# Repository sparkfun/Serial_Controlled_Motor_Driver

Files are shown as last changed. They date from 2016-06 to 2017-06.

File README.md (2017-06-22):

SparkFun Serial Controlled Motor Driver
=======================================

SparkFun Serial Controlled Motor Driver

[*SparkFun Serial Controlled Motor Driver (ROB-13911)*](https://www.sparkfun.com/products/13911)

The expandable SparkFun Serial Controlled Motor Driver allows you to control 2 DC motors using a serial command interface over I2C, SPI, or TTL UART. 

Features:
* User port configurable to SPI, I2C, or UART.
* Expansion port utalizing I2C that allows 16 additional drivers
* Auto-enumeration based on connection of expansion 'In' and 'Out' connections - First board becomes first slave in software.
* 1.5 A peak drive per channel
* Bridging mode for any one board to double current drive.
* Operates from 3 to 11 volts with 12v absolute max.
* Stock 3.3v operation of cpu and signals, with VCC breakable to allow up to 5.5v levels.

Repository Contents
-------------------
* **/Documentation** - Datasheet, test information, and diagrams
* **/Firmware** - PSoC projects of embedded firmware
* **/Hardware** - Eagle design files (.brd, .sch)
* **/Libraries** - Libraries for use with the motor driver
* **/Production** - Production files
* **/Software** - Arduino sketches and examples

Documentation
--------------
* **[Library](https://github.com/sparkfun/SparkFun_Serial_Controlled_Motor_Driver_Arduino_Library)** - Arduino library
* **[Hookup Guide](https://learn.sparkfun.com/tutorials/serial-controlled-motor-driver-hookup-guide)** - Basic hookup guide
* **[SparkFun Fritzing repo](https://github.com/sparkfun/Fritzing_Parts)** - Fritzing diagrams for SparkFun products.
* **[SparkFun 3D Model repo](https://github.com/sparkfun/3D_Models)** - 3D models of SparkFun products. 
* **[SparkFun Graphical Datasheets](https://github.com/sparkfun/Graphical_Datasheets)** -Graphical Datasheets for various SparkFun products.

Hardware Compatibility
----------------
* [ROB-13911](https://www.sparkfun.com/products/13911) - Serial controlled motor driver.
* [DEV-14213](https://www.sparkfun.com/products/14213) - SparkFun moto:bit (SCMD_FID_V07a.HEX).

Version History
---------------
* [HW_1.2_FW_1.2](https://github.com/sparkfun/Serial_Controlled_Motor_Driver/tree/HW_1.2_FW_1.2) - Original product
* [V_1.5](https://github.com/sparkfun/Serial_Controlled_Motor_Driver/tree/V_1.5) - Revision prototype 1
* [V_1.6](https://github.com/sparkfun/Serial_Controlled_Motor_Driver/tree/V_1.6) - Revision prototype 2
* [V_1.6.1](https://github.com/sparkfun/Serial_Controlled_Motor_Driver/tree/V_1.6.1) - Revision prototype 2 with non-zero width poly outlines and dev board version V_1.X
* [V_2.0](https://github.com/sparkfun/Serial_Controlled_Motor_Driver/tree/V_2.0) - Version 2.0 of product
* [V_2.0.1](https://github.com/sparkfun/Serial_Controlled_Motor_Driver/tree/V_2.0.1) - Compatible with moto:bit hardware.

License Information
-------------------

This product is _**open source**_! 

Please review the LICENSE.md file for license information. 

If you have any questions or concerns on licensing, please contact techsupport@sparkfun.com.

Distributed as-is; no warranty is given.

- Your friends at SparkFun.

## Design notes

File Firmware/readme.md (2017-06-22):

Contents
-----------

* SCMD_FW.cydsn -- Project folder for current version of firmware.
* Releases -- hex files for release
  * SCMD_FID_02.hex -- Internal release, lacks self diagnostics features
  * SCMD_FID_03.hex -- Beta release.  Final release features present.  Now has better failsafe, control of config_pin, bus rate control regs and is tested on all three interface modes.
  * SCMD_FID_04.hex -- Test mode for config pins added, enumeration status added, high speed uart modes added as jumper settings.
  * SCMD_FID_06.hex -- Production release.
  * SCMD_FID_07.hex -- Release for moto:bit compatibility.
  * SCMD_FID_07a.hex -- Production release for moto:bit compatibility.  Fixed enable pin bit (was b2, now is b4).

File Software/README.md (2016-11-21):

SparkFun Serial Controlled Motor Driver (SCMD) Software
=======================================

This software used to test the firmware and functions.  Users should see directory /Libraries (up one level) for example code and arduino libraries.

Contents:
-------------------
* /FailSafeTest/ -- Configures the SCMD into a mode to allow failsafe testing
* /FWFunctionalTest/ -- Automated portion of the functional test doc
* /testProgram/ -- Program used in product video with sliders

License Information
-------------------
The hardware is released under [Creative Commons ShareAlike 4.0 International](https://creativecommons.org/licenses/by-sa/4.0/).
The code is beerware; if you see me (or any other SparkFun employee) at the local, and you've found our code helpful, please buy us a round!

Distributed as-is; no warranty is given.

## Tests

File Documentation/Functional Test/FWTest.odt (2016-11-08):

# Buses

## Test the I2C user interface

This test checks all the ways a user can connect the I2C interface.

Procedure:

1. Test the following configurations:
  1. SCMD master at any lowest address, 100 kHz redboard Pass
  2. Two SCMD masters, one at highest address, 100 KHz redboard Pass
  3. 400 KHz on teensy (Low priority) Skipped
2. For each configuration, run the diag example and look for errors. Pass

Criteria:

1. Did the EUTs behave normally?? YES

## Test the SPI user interface

This test checks all the ways a user can connect the SPI interface.

Procedure:

1. Test the following configurations:
  1. SCMD master at 1 MHz Tested at 500kHz and 1 MHz, Pass
  2. Two SCMD masters with different CS pins. Pass
2. For each configuration, run the diag example and look for errors. Pass

Criteria:

2. Did the EUTs behave normally? YES

## Test the UART user interface

Procedure:

1. Test the following configurations:
  1. SCMD at default baud Pass
  2. SCMD at 57600 baud by jumper Pass
  3. SCMD at 115200 baud by jumper Pass
  4. Other configurations by using the commands U0-U7. Pass
2. Test that the number are accepted as 1 or two digit for most, and 3 for drive percent Pass
3. Test that enable is passed to slaves Pass
4. Test that E, B, and MxxS commands result in the proper bit flipped within INV_X_X, BRIDGE_SLV_X registers Pass

#define SCMD_INV_2_9 0x50

#define SCMD_INV_10_17 0x51

#define SCMD_INV_18_25 0x52

#define SCMD_INV_26_33 0x53

#define SCMD_BRIDGE_SLV_L 0x54

#define SCMD_BRIDGE_SLV_H 0x55

Criteria:

1. Did the EUTs behave normally?? YES

# FW elements

For these tests, connect 16 slaves and perform the following actions using the registerRWtool

## Test motor driving registers

Make sure motor information is passed to the correct locations

Procedure:

1. Test that the following motors drive when master locations are written: Pass
  1. motor 0,1, 2, 3, 4, 5, 17, 18, and 33

Criteria:

1. Do commands cause correct change on all motors? YES

## Test slave configuration

Test that writing to slave and global registers passes the information on to the slaves correctly. For these tests remote access is required by remote window or arduino function.

1. Motor 2, 9, 10, 17, 18, 25, 26 and 33 Pass
2. Bridge 0, 1, 8, 9, and 16 Pass

#define SCMD_MOTOR_A_INVERT 0x12

#define SCMD_MOTOR_B_INVERT 0x13

#define SCMD_BRIDGE 0x14

Procedure:

1. Write a pattern to INV regs and read remote local inversion regs. Pass
2. Write a pattern to BRIDGE regs and read remote local bridging regs Pass
3. Check that the following are passed directly (global config) to the associated local slave registers.
  1. DRIVER_ENABLE Pass
  2. MASTER_LOCK Pass
  3. USER_LOCK Pass
  4. FSAFE_TIME Pass

Criteria:

1. Are all values passed correctly? YES

## Check lock protections

Make sure the master and user locks operate

Procedure:

1. Write each "R" register with master key removed, then use REG_OOR_CNT to verify if they were protected Pass
2. Write each "user lock"able register with the user key removed, then use REG_OOR_CNT to verify they did not accept the data. Pass
3. Write each "user lock"able register with the user key inserted, REG_OOR_CNT should read 0. Pass
4. Write a new FID in with both keys inserted, and read back to verify. Pass

Criteria:

1. Were the locks capible of preventing or allowing the correct operations? YES

## Test the failsafe mode

This checks that all modes of failsafe operate

Procedure:

1. Probe config out and exp. data
2. Set the FSAFE_TIME(0x76) to 0xC8 for 2 second failsafe time Pass
3. Set FSAFE_CTRL:
  1. Use b1 for drive off/last behavior Pass
  2. Set 0x02 for reboot Pass
  3. Set 0x04 for re-enumerate. Pass
  4. Set 0x08 for user port re-init. Pass – works but doesn't recover data
  5. Set 0x10 for expansion port re-init Pass
4. Check the slave contents of FSAFE_TIME to determine if configuration was properly transfered during re-enumerate. Yes

Criteria:

1. Did the EUT recover as expected? Yes

## Test enumeration

Check that enumeration occurs correctly. For many of these, reading 0x0B for top address may be useful.

Procedure:

1. Check that enumeration occurs successfully for 0, 1, 2, and 16 slaves. Pass
2. Issue a reboot by CONTROL_1 for 16 Pass
3. Configure some global settings
4. Issue a re-enumeration by CONTROL_1 for 16 slaves
5. Check that global settings were correctly passed to slaves Pass
6. Configure master config in pin with MST_E_IN_FN and test function by shorting config_in to ground Pass

Criteria:

1. Does the top address match for various slaves? YES?
2. Do both reboots result in a proper enumeration? YES?
3. Do both reenumerations result in the correct configuration? YES?

## Test the expansion bus speed setting

Check that the expansion bus can be configured by inspecting with a scope.

Procedure:

1. Measure the bit rate of the defualt 100KHz setting
2. Configure and test the 50KHz and 400 KHz settings using E_BUS_SPEED
3. Measure the slave motor data packets dead time, and set UPDATE_RATE to change Pass
4. With UPDATE_RATE set to 0, does a packet occur after writing FORCE_UPDATE to 1? Pass

Criteria:

1. Are bus configuration parameters effecting operation properly? YES

## Test an item in the Test Plan

Describe the intent of the item to be tested

Procedure:

1. First step to testing
2. Second step to testing

Criteria:

1. Describe acceptable test results as a question? YES/NO

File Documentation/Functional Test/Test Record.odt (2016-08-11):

# Functional Test Record

## 1) Test thermal performance of the board and DRV8835

Determine temperature rise of board operating at max drive

Procedure:

1. Attach resistors to output channels such that they consume 1.5A at 11.0V supply
2. Attach termocouple to DRV8835
3. Lay EUT flat on FR4 "burn surface", or something with marginal thermal conductivity. Allow top-side convection.
4. Target FliR cam at EUT
5. Starting with low drive,
  1. Set drive level
  2. Measure current at that drive level
  3. Wait for EUT to stabilize
  4. Record final temperature of DRV8835
  5. Take a thermal picture
  6. Increment drive level

Criteria:

1. Unknown – Does EUT satisfy typical use cases? YES/NO

## 2) Input Voltage Range

Check that the EUT operates normally under the full voltage range of the product, under various loads

Procedure:

1. Attach current and voltage meters to input
2. Power the EUT with variable supply
3. Attach voltage monitor to VREG pin
4. Program the device to output 0.5A, 1A, 1.5 A total drive (channels combined)
5. Operate the drive on both channels while measuring the VREG pin, input current, and input voltage. Create a graph

Criteria:

1. Does the EUT function as expected? YES/NO
2. Is the output voltage liner to drive at all levels? YES/NO

## 3) Test Current Resistance in board

Determine if the PCB is limiting current to the board

Procedure:

1. Measure input voltage and current, apply 11.0V
2. Attach 11.0 V resistors to output terminals
3. Drive both outputs max each way.

Criteria:

1. Do both outputs deliver 1.5A? YES/NO

## 4) Test LDO power dissipation

Calculate the power dissipated by the LDO

Procedure:

1. Split the power out trace on the bottom of the board near the VREG pin, insert current meter
2. Measure voltage in, current in, voltage out(VREG), current out
3. Take measurements across voltage range in 1v increments
4. Produce a graph of the power consumed by the LDO

Criteria:

1. Is the power dissipated less than 1/4 watt? YES/NO

## 5) Determine resistance to back-EMF generated by manually pushed motors

Test that forcing the drive motors around during drive does not damage the EUT

Procedure:

1. Supply the EUT through a 0.5 to 1.0 ohm resistor, RECORD VALUE HERE
2. Attach a scope to VREG and VIN
3. Attach motors to output drives
4. Do the following for 3.0V, 6.0V, and 11.0V supply levels
  1. Increment the drive levels
  2. Spin and mess with the motors
  3. Record peaks levels from scope
5. Capture 1 or more

Criteria:

1. Do the levels stay within absolute maximums? YES/NO
2. Does the EUT continue to operate normally? YES/NO

## Test an item in the Test Plan

Describe the intent of the itme to be tested

Procedure:

1. First step to testing
2. Second step to testing

Criteria:

1. Describe acceptable test results as a question? YES/NO

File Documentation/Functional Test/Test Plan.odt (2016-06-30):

# Functional Test Plan

## Code Things to verify

- SPI operation
- SPI API for arduino
- I2C operation
- I2C API for arduino
- Asyncronous serial operation
- Timing between slaves and masters
- Bus enumeration
- Config bit operation

## HW things to verify

- Input voltage range
- Input current range
- LDO power dissipation
- Temperature rise at full power, both channels
- Nominal recommended confined current limit
- Duribility to back-EMF
  - At zero drive
  - At positive max drive
  - At negitive max drive

## Things to consider

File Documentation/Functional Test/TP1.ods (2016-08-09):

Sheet: Graphs
0.5oz, no sink
0.5oz, no air
0.5oz, convection
2.0oz, no sink
2.0oz, convection
2.0oz, Forced Air

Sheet: No Airflow_0.5oz
No heatsink, loosly clamped to burn table at psoc
 | Drive IA | Drive IB | Stable T | Time | Notes
 | 0.000 | 0.000 | 31 | 10
 | 0.190 | 0.195 | 34.22 | 180
 | 0.410 | 0.412 | 43.22 | 375
 | 0.590 | 0.601 | 56.72 | 650
 | 0.830 | 0.795 | 77.97 | 955
 | 0.980 | 1.001 | 104.47 | 1290 | Kinda gave up ramp

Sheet: Heatsink_FlatDown_0.5oz
With small heatsink, pins pointed down on burn table
 | Drive IA | Drive IB | Stable T | Time | Notes
 | 0.000 | 0.000 | 31.000 | 10
 | 0.190 | 0.194 | 33.970 | 1635
 | 0.410 | 0.403 | 41.720 | 1840
 | 0.590 | 0.603 | 52.970 | 2055
 | 0.810 | 0.801 | 70.470 | 2280
 | 0.990 | 1.160 | 94.220 | 2630
 | 1.190 | 1.211 | 116.470 | 2700 | Gave up early – may hit 120
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

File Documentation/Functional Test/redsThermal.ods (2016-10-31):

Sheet: Graphs
No heat sink
TO220 heat sink
Forced air, No heat sink
TO220
2.0oz, convection

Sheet: Flat, no sink
No heatsink, loosly clamped to burn table at psoc
Total Drive | Drive IA | Drive IB | Stable T | Time | Notes
0 | 0.000 | 0.000 | 26.22 | 525
0.4 | 0.210 | 0.190 | 29.47 | 3850
0.81 | 0.410 | 0.400 | 40.47 | 1030
1.2 | 0.600 | 0.600 | 54.97 | 5030
1.59 | 0.800 | 0.790 | 73.22 | 5410
1.99 | 1.000 | 0.990 | 96.72 | 5880

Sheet: Flat, TO220
With small heatsink, pins pointed down on burn table
Total Drive | Drive IA | Drive IB | Stable T | Time | Notes
0 | 0.000 | 0.000 | 25.970 | 6870
0.4 | 0.210 | 0.190 | 29.470 | 7785
0.8 | 0.390 | 0.410 | 38.220 | 8465
1.19 | 0.590 | 0.603 | 49.970 | 9550
1.59 | 0.800 | 0.790 | 64.220 | 10205
1.99 | 0.990 | 1.000 | 82.970 | 10760
2.39 | 1.200 | 1.190 | 109.720 | 11330
 | 1.190 | 1.211 | 116.470 | 2700 | Gave up early – may hit 120
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

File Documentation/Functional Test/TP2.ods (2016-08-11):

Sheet: Sheet1
Load 1 |  |  |  |  |  |  |  |  |  |  | Load 2 |  |  |  |  |  |  |  |  |  |  | Load 3
Vin | Iin | Calc Pin | Vl | Il | Vl | Il | PA | PB | Vcc | Icc | Vin | Iin | Calc Pin | Vl | Il | Vl | Il | PA | PB | Vcc | Icc | Vin | Iin | Calc Pin | Vl | Il | Vl | Il | PA | PB | Vcc | Icc
2.980 | 0.140 |  | 0.515 | 0.234 | 0.471 | 0.240 |  |  | 2.940 | 0.009 | 2.960 | 0.430 |  | 0.891 | 0.439 | 0.876 | 0.450 |  |  | 2.936 | 0.009
4.990 | 0.100 |  | 0.551 | 0.266 | 0.528 | 0.270 |  |  | 3.300 | 0.009 | 4.970 | 0.300 |  | 1.006 | 0.502 | 0.984 | 0.510 |  |  | 3.300 | 0.009 | 4.950 | 0.650 |  | 1.528 | 0.765 | 1.440 | 0.740 |  |  | 3.300 | 0.009
7.470 | 0.070 |  | 0.511 | 0.257 | 0.485 | 0.240 |  |  | 3.300 | 0.009 | 7.490 | 0.210 |  | 0.999 | 0.505 | 1.012 | 0.520 |  |  | 3.301 | 0.009 | 7.440 | 0.430 |  | 1.516 | 0.757 | 1.442 | 0.740 |  |  | 3.301 | 0.009
10.010 | 0.070 |  | 0.514 | 0.251 | 0.522 | 0.260 |  |  | 3.301 | 0.009 | 10.000 | 0.170 |  | 1.038 | 0.525 | 0.955 | 0.490 |  |  | 3.301 | 0.009 | 9.990 | 0.350 |  | 1.495 | 0.764 | 1.467 | 0.760 |  |  | 3.301 | 0.009
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

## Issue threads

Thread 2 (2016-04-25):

PROD_IDs needed

SFE-KADE, 2016-04-25:
Both the cypress chip and the DRV chip have incorrect prod_ids

marshalltaylorSFE, 2016-04-26:
One updated, the other was actually a problem with the bom

Closed 2016-04-26.

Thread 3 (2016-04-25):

Vreg not included on BOM

SFE-KADE, 2016-04-25:

marshalltaylorSFE, 2016-04-26:
Fixed

Closed 2016-04-26.

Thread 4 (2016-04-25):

Is the version number correct

SFE-KADE, 2016-04-25:
I think the changes for this revision are significant enough to warrant a bump to "V2".

marshalltaylorSFE, 2016-04-26:
Product will jump to V2 at reds level.  Chose to start at 1.5 as we'll most likely have a few protos.  I'm avoiding having a bunch of boards hanging out with v20 on them but different hardware.

Closed 2016-04-26.

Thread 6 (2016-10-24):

NC, SCL pin silk error

marshalltaylorSFE, 2016-10-24:
The User Port pin labeled 'NC, SCL' is no connect or SPI clock, and should be called 'NC, SCK' instead.

ToniCorinne, 2016-11-18:
This issue has been marked in Sparkle and FoTR has been notified.

Closed 2016-11-18.

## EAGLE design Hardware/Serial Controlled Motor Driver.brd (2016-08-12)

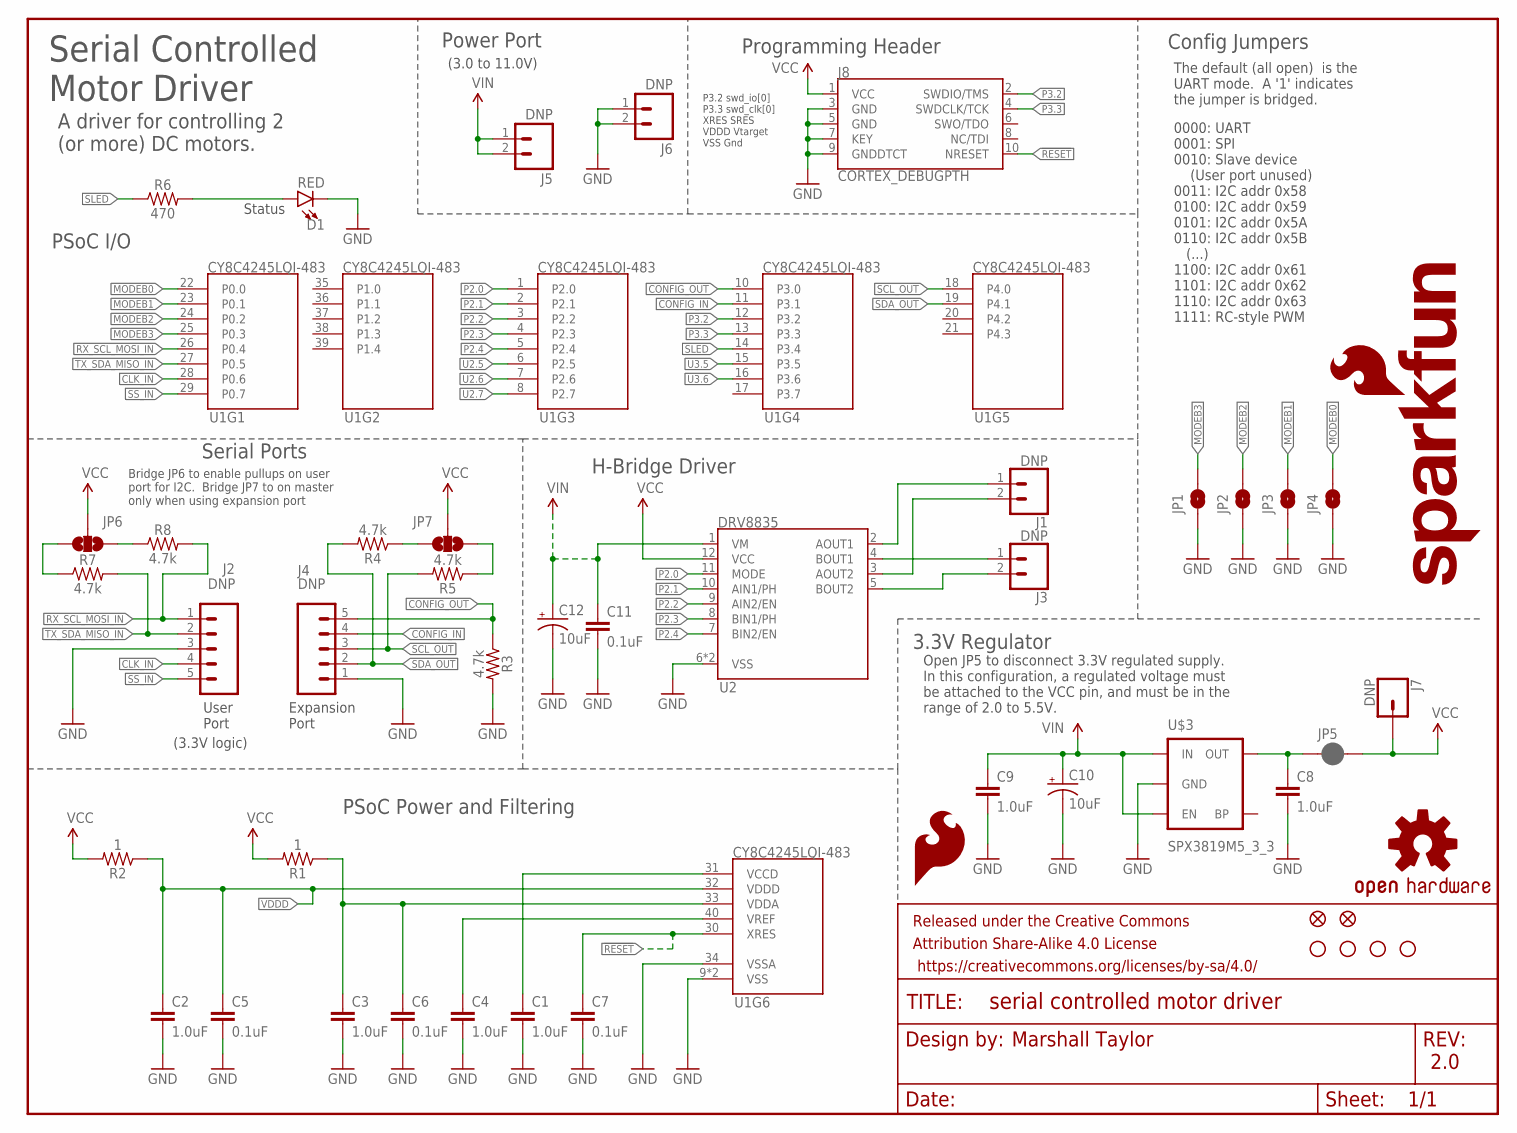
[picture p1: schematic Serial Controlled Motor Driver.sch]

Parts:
C1, C2, C3, C4, C8, C9: 1.0uF; 0402
C5, C6, C7, C11: 0.1uF; 0402
C10, C12: 10uF; EIA3216
D1: RED; LED-0603
FD1, FD2: FIDUCIALUFIDUCIAL; MICRO-FIDUCIAL
FRAME1: FRAME-LETTER; CREATIVE_COMMONS
H1, H2, H3, H4: STAND-OFF
J1, J3: DNP; 1X02_NO_SILK
J2, J4: DNP; 1X05
J5, J6: DNP; 1X02@1
J7: DNP; 1X01
J8: CORTEX_DEBUGPTH; 2X5-PTH-1.27MM
JP1, JP2, JP3, JP4: JUMPER-PAD-2; PAD-JUMPER-2-NO_YES_SILK
JP5: JUMPER-PAD-2; PAD-JUMPER-2-NC_BY_PASTE_YES_SILK
JP6, JP7: JUMPER-PAD-3-NOYES_SILK; PAD-JUMPER-3-NO_YES_SILK
LOGO1: SFE_LOGO_FLAME.1_INCH; SFE_LOGO_FLAME_.1
LOGO2: OSHW-LOGOMINI; OSHW-LOGO-MINI
LOGO3: SFE_LOGO_NAME_FLAME.1_INCH; SFE_LOGO_NAME_FLAME_.1
R1, R2: 1; 0603
R3, R4, R5, R7, R8: 4.7k; 0603
R6: 470; 0603
U1: CY8C4245LQI-483; QFN-40
U2: DRV8835; WSON-12
U$3: SPX3819M5_3_3; SOT-23-5-VREG

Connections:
!RESET: C7.1, J8.10 (NRESET), U1.30 (XRES)
AOUT1: J1.1, U2.2 (AOUT1)
AOUT2: J1.2, U2.3 (AOUT2)
BOUT1: J3.1, U2.4 (BOUT1)
BOUT2: J3.2, U2.5 (BOUT2)
CLK_IN: J2.4, U1.28 (P0.6)
CONFIG_IN: J4.4, U1.11 (P3.1)
CONFIG_OUT: J4.5, R3.1, U1.10 (P3.0)
GND: C1.2, C2.2, C3.2, C4.2, C5.2, C6.2, C7.2, C8.2, C9.2, C10.-, C11.2, C12.-, D1.C, J2.3, J4.1, J6.1, J6.2, J8.3 (GND), J8.5 (GND), J8.7 (KEY), J8.9 (GNDDTCT), JP1.1, JP2.1, JP3.1, JP4.1, R3.2, U1.9 (VSS), U1.34 (VSSA), U1.EP (VSS), U2.6 (VSS), U2.PAD (VSS), U$3.2 (GND)
MODEB0: JP4.2, U1.22 (P0.0)
MODEB1: JP3.2, U1.23 (P0.1)
MODEB2: JP2.2, U1.24 (P0.2)
MODEB3: JP1.2, U1.25 (P0.3)
unnamed: C1.1, U1.31 (VCCD)
unnamed: JP7.1, R4.1
unnamed: C3.1, C6.1, R1.1, U1.33 (VDDA)
unnamed: C4.1, U1.40 (VREF)
unnamed: C8.1, JP5.1, U$3.5 (OUT)
unnamed: JP7.3, R5.1
unnamed: D1.A, R6.2
unnamed: JP6.1, R8.1
unnamed: JP6.3, R7.1
P2.0: U1.1 (P2.0), U2.11 (MODE)
P2.1: U1.2 (P2.1), U2.10 (AIN1/PH)
P2.2: U1.3 (P2.2), U2.9 (AIN2/EN)
P2.3: U1.4 (P2.3), U2.8 (BIN1/PH)
P2.4: U1.5 (P2.4), U2.7 (BIN2/EN)
P3.2: J8.2 (SWDIO/TMS), U1.12 (P3.2)
P3.3: J8.4 (SWDCLK/TCK), U1.13 (P3.3)
RX_SCL_MOSI_IN: J2.1, R8.2, U1.26 (P0.4)
SCL_OUT: J4.3, R5.2, U1.18 (P4.0)
SDA_OUT: J4.2, R4.2, U1.19 (P4.1)
SLED: R6.1, U1.14 (P3.4)
SS_IN: J2.5, U1.29 (P0.7)
TX_SDA_MISO_IN: J2.2, R7.2, U1.27 (P0.5)
U2.5: U1.6 (P2.5)
U2.6: U1.7 (P2.6)
U2.7: U1.8 (P2.7)
U3.5: U1.15 (P3.5)
U3.6: U1.16 (P3.6)
VCC: J7.1, J8.1 (VCC), JP5.2, JP6.2, JP7.2, R1.2, R2.2, U2.12 (VCC)
VDDD: C2.1, C5.1, R2.1, U1.32 (VDDD)
VIN: C9.1, C10.+, C11.1, C12.+, J5.1, J5.2, U2.1 (VM), U$3.1 (IN), U$3.3 (EN)

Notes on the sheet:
PSoC Power and Filtering
Serial Controlled Motor Driver
Config Jumpers
Marshall Taylor
PSoC I/O
3.3V Regulator
2.0
P3.2 swd_io[0] P3.3 swd_clk[0] XRES SRES VDDD Vtarget VSS Gnd
Serial Ports
Power Port
Programming Header
H-Bridge Driver
A driver for controlling 2 (or more) DC motors.
0000: UART 0001: SPI 0010: Slave device (User port unused) 0011: I2C addr 0x58 0100: I2C addr 0x59 0101: I2C addr 0x5A 0110: I2C addr 0x5B (...) 1100: I2C addr 0x61 1101: I2C addr 0x62 1110: I2C addr 0x63 1111: RC-style PWM
The default (all open) is the UART mode. A '1' indicates the jumper is bridged.
Status
(3.0 to 11.0V)
Expansion Port
User Port
Open JP5 to disconnect 3.3V regulated supply. In this configuration, a regulated voltage must be attached to the VCC pin, and must be in the range of 2.0 to 5.5V.
Bridge JP6 to enable pullups on user port for I2C. Bridge JP7 to on master only when using expansion port
(3.3V logic)

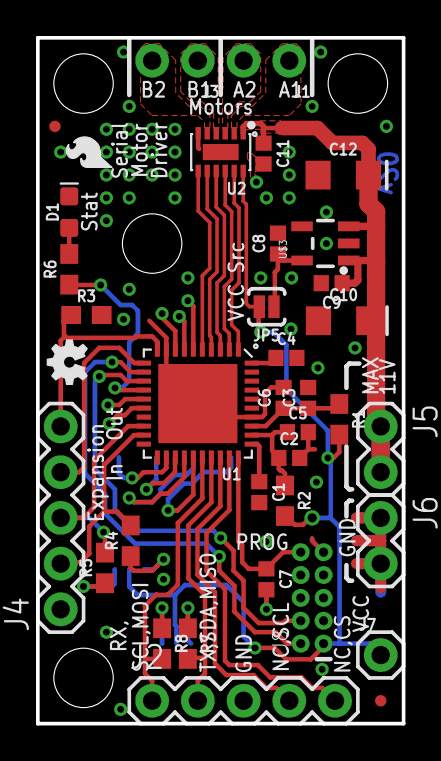
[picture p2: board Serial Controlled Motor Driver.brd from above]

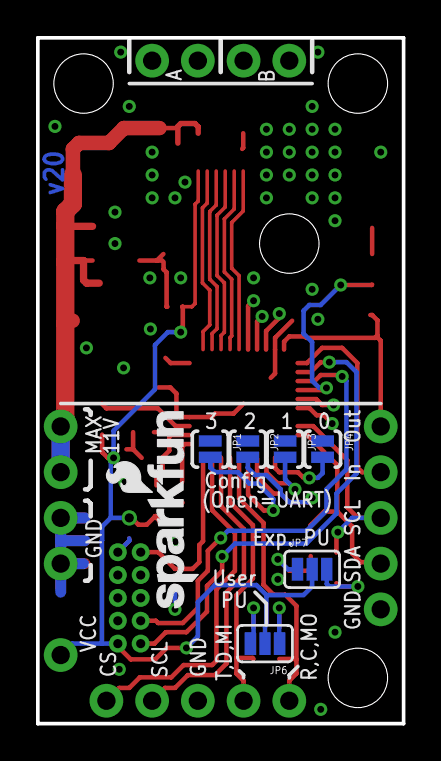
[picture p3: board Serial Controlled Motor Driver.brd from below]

Board: 2 copper layers, 20.3 x 38.1 mm, 49 parts (7 on the bottom side), 38 nets.

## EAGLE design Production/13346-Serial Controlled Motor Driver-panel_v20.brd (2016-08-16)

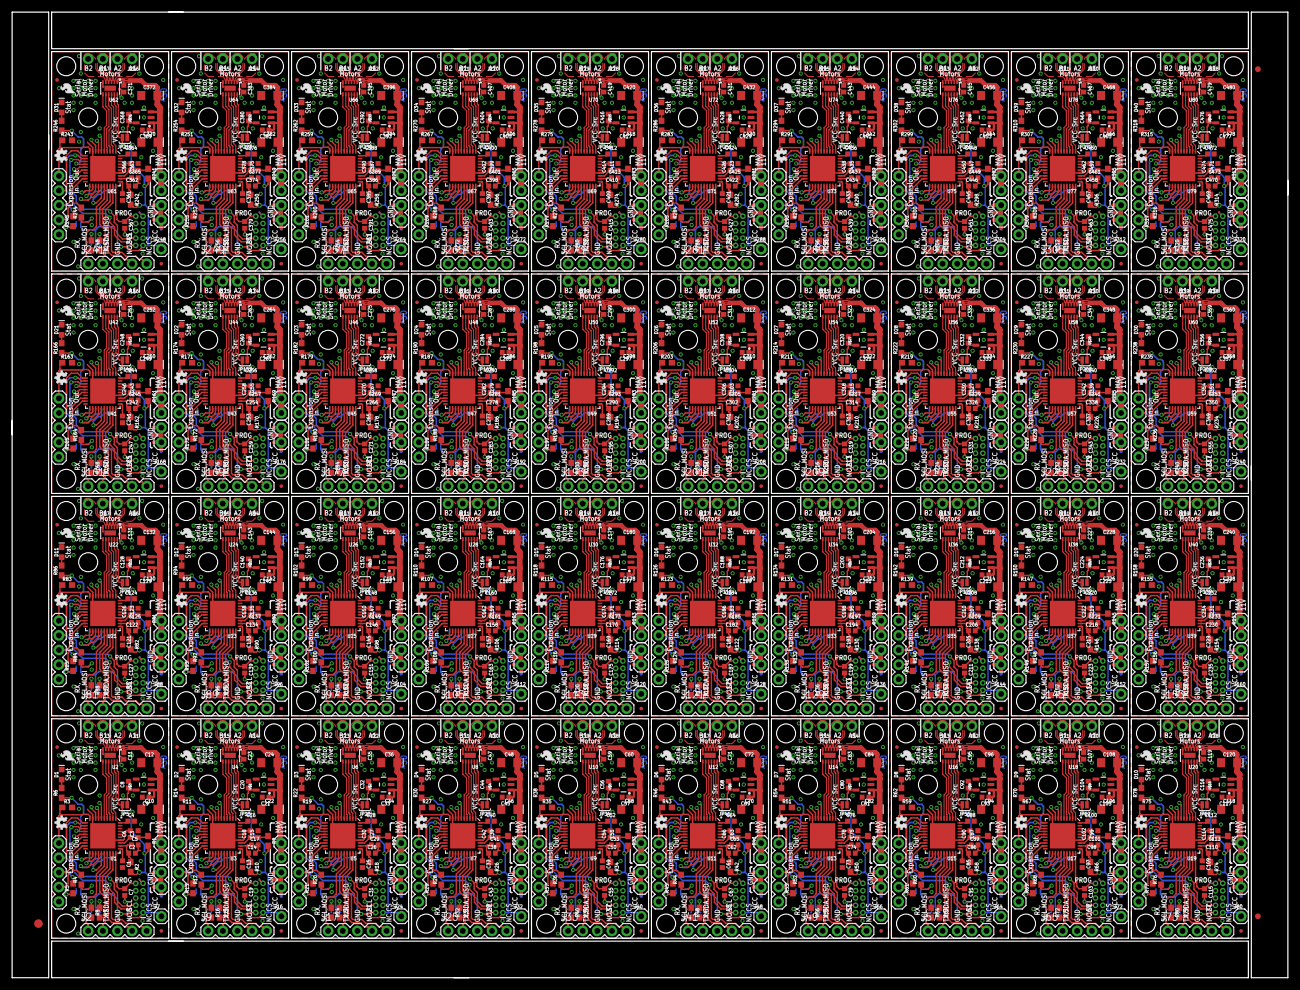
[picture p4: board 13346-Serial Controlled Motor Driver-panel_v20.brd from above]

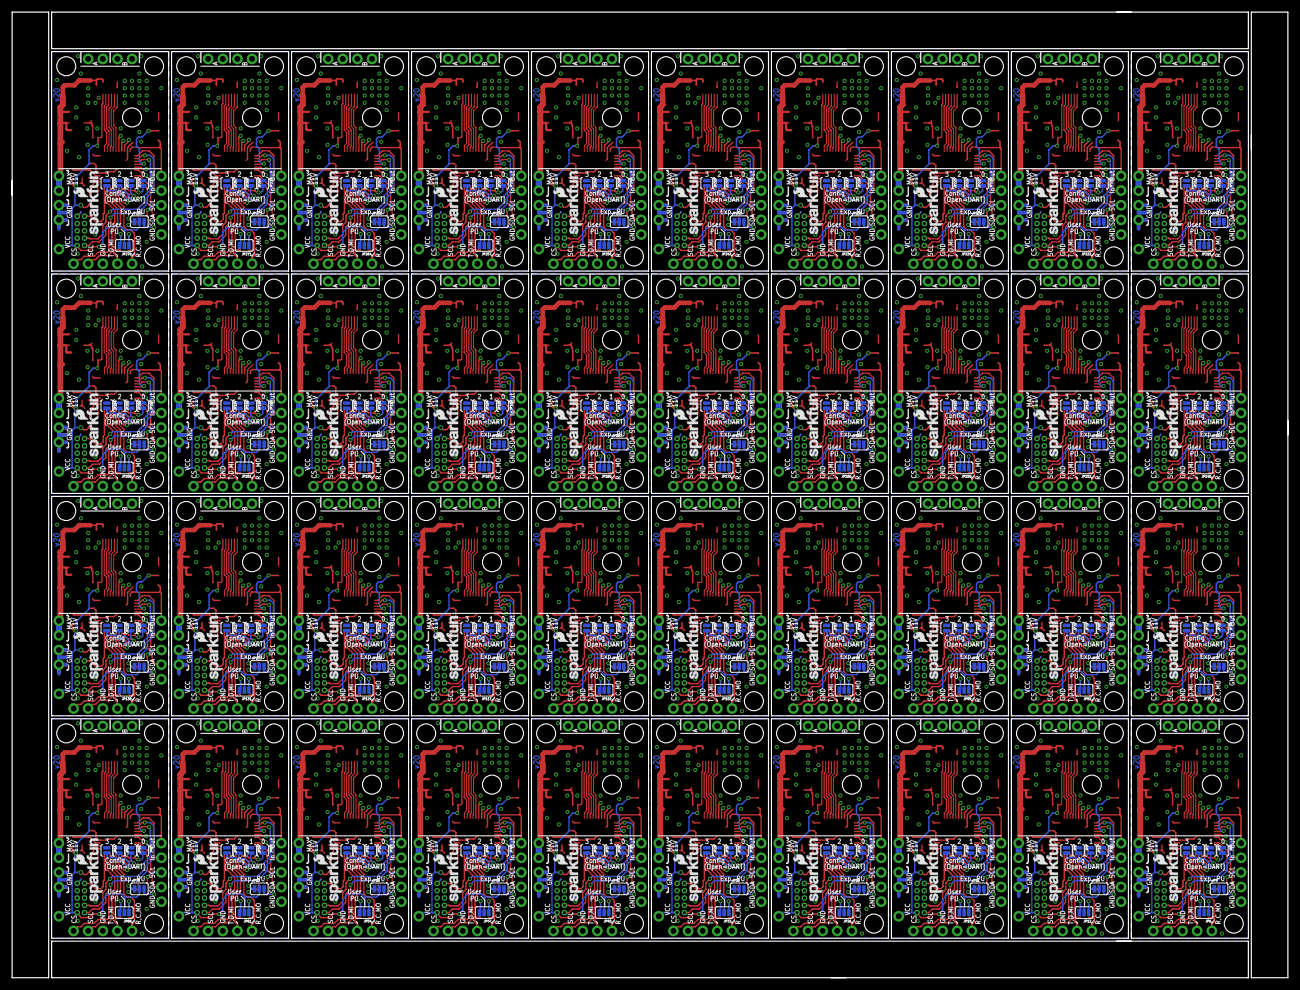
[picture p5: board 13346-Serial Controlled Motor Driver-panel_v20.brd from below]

Board: 2 copper layers, 221.5 x 167.6 mm, 1923 parts (280 on the bottom side), 1520 nets.

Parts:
C1, C2, C3, C4, C8, C9, C13, C14, C15, C16, C20, C21, C25, C26, C27, C28, C32, C33, C37, C38, C39, C40, C44, C45, C49, C50, C51, C52, C56, C57, C61, C62, C63, C64, C68, C69, C73, C74, C75, C76, C80, C81, C85, C86, C87, C88, C92, C93, C97, C98, C99, C100, C104, C105, C109, C110, C111, C112, C116, C117, C121, C122, C123, C124, C128, C129, C133, C134, C135, C136, C140, C141, C145, C146, C147, C148, C152, C153, C157, C158, C159, C160, C164, C165, C169, C170, C171, C172, C176, C177, C181, C182, C183, C184, C188, C189, C193, C194, C195, C196, C200, C201, C205, C206, C207, C208, C212, C213, C217, C218, C219, C220, C224, C225, C229, C230, C231, C232, C236, C237, C241, C242, C243, C244, C248, C249, C253, C254, C255, C256, C260, C261, C265, C266, C267, C268, C272, C273, C277, C278, C279, C280, C284, C285, C289, C290, C291, C292, C296, C297, C301, C302, C303, C304, C308, C309, C313, C314, C315, C316, C320, C321, C325, C326, C327, C328, C332, C333, C337, C338, C339, C340, C344, C345, C349, C350, C351, C352, C356, C357, C361, C362, C363, C364, C368, C369, C373, C374, C375, C376, C380, C381, C385, C386, C387, C388, C392, C393, C397, C398, C399, C400, C404, C405, C409, C410, C411, C412, C416, C417, C421, C422, C423, C424, C428, C429, C433, C434, C435, C436, C440, C441, C445, C446, C447, C448, C452, C453, C457, C458, C459, C460, C464, C465, C469, C470, C471, C472, C476, C477: 1.0uF; 0402
C5, C6, C7, C11, C17, C18, C19, C23, C29, C30, C31, C35, C41, C42, C43, C47, C53, C54, C55, C59, C65, C66, C67, C71, C77, C78, C79, C83, C89, C90, C91, C95, C101, C102, C103, C107, C113, C114, C115, C119, C125, C126, C127, C131, C137, C138, C139, C143, C149, C150, C151, C155, C161, C162, C163, C167, C173, C174, C175, C179, C185, C186, C187, C191, C197, C198, C199, C203, C209, C210, C211, C215, C221, C222, C223, C227, C233, C234, C235, C239, C245, C246, C247, C251, C257, C258, C259, C263, C269, C270, C271, C275, C281, C282, C283, C287, C293, C294, C295, C299, C305, C306, C307, C311, C317, C318, C319, C323, C329, C330, C331, C335, C341, C342, C343, C347, C353, C354, C355, C359, C365, C366, C367, C371, C377, C378, C379, C383, C389, C390, C391, C395, C401, C402, C403, C407, C413, C414, C415, C419, C425, C426, C427, C431, C437, C438, C439, C443, C449, C450, C451, C455, C461, C462, C463, C467, C473, C474, C475, C479: 0.1uF; 0402
C10, C12, C22, C24, C34, C36, C46, C48, C58, C60, C70, C72, C82, C84, C94, C96, C106, C108, C118, C120, C130, C132, C142, C144, C154, C156, C166, C168, C178, C180, C190, C192, C202, C204, C214, C216, C226, C228, C238, C240, C250, C252, C262, C264, C274, C276, C286, C288, C298, C300, C310, C312, C322, C324, C334, C336, C346, C348, C358, C360, C370, C372, C382, C384, C394, C396, C406, C408, C418, C420, C430, C432, C442, C444, C454, C456, C466, C468, C478, C480: 10uF; EIA3216
D1, D2, D3, D4, D5, D6, D7, D8, D9, D10, D11, D12, D13, D14, D15, D16, D17, D18, D19, D20, D21, D22, D23, D24, D25, D26, D27, D28, D29, D30, D31, D32, D33, D34, D35, D36, D37, D38, D39, D40: RED; LED-0603
E$1: FIDUCIAL-1.5X3
E$5, E$6: FIDUCIAL-1X2
FD1, FD2, FD3, FD4, FD5, FD6, FD7, FD8, FD9, FD10, FD11, FD12, FD13, FD14, FD15, FD16, FD17, FD18, FD19, FD20, FD21, FD22, FD23, FD24, FD25, FD26, FD27, FD28, FD29, FD30, FD31, FD32, FD33, FD34, FD35, FD36, FD37, FD38, FD39, FD40, FD41, FD42, FD43, FD44, FD45, FD46, FD47, FD48, FD49, FD50, FD51, FD52, FD53, FD54, FD55, FD56, FD57, FD58, FD59, FD60, FD61, FD62, FD63, FD64, FD65, FD66, FD67, FD68, FD69, FD70, FD71, FD72, FD73, FD74, FD75, FD76, FD77, FD78, FD79, FD80: FIDUCIALUFIDUCIAL; MICRO-FIDUCIAL
H1, H2, H3, H4, H5, H6, H7, H8, H9, H10, H11, H12, H13, H14, H15, H16, H17, H18, H19, H20, H21, H22, H23, H24, H25, H26, H27, H28, H29, H30, H31, H32, H33, H34, H35, H36, H37, H38, H39, H40, H41, H42, H43, H44, H45, H46, H47, H48, H49, H50, H51, H52, H53, H54, H55, H56, H57, H58, H59, H60, H61, H62, H63, H64, H65, H66, H67, H68, H69, H70, H71, H72, H73, H74, H75, H76, H77, H78, H79, H80, H81, H82, H83, H84, H85, H86, H87, H88, H89, H90, H91, H92, H93, H94, H95, H96, H97, H98, H99, H100, H101, H102, H103, H104, H105, H106, H107, H108, H109, H110, H111, H112, H113, H114, H115, H116, H117, H118, H119, H120, H121, H122, H123, H124, H125, H126, H127, H128, H129, H130, H131, H132, H133, H134, H135, H136, H137, H138, H139, H140, H141, H142, H143, H144, H145, H146, H147, H148, H149, H150, H151, H152, H153, H154, H155, H156, H157, H158, H159, H160: STAND-OFF
J1, J3, J14, J15, J22, J23, J30, J31, J38, J39, J46, J47, J54, J55, J62, J63, J70, J71, J78, J79, J86, J87, J94, J95, J102, J103, J110, J111, J118, J119, J126, J127, J134, J135, J142, J143, J150, J151, J158, J159, J166, J167, J174, J175, J182, J183, J190, J191, J198, J199, J206, J207, J214, J215, J222, J223, J230, J231, J238, J239, J246, J247, J254, J255, J262, J263, J270, J271, J278, J279, J286, J287, J294, J295, J302, J303, J310, J311, J318, J319: DNP; 1X02_NO_SILK
J2, J4, J9, J10, J17, J18, J25, J26, J33, J34, J41, J42, J49, J50, J57, J58, J65, J66, J73, J74, J81, J82, J89, J90, J97, J98, J105, J106, J113, J114, J121, J122, J129, J130, J137, J138, J145, J146, J153, J154, J161, J162, J169, J170, J177, J178, J185, J186, J193, J194, J201, J202, J209, J210, J217, J218, J225, J226, J233, J234, J241, J242, J249, J250, J257, J258, J265, J266, J273, J274, J281, J282, J289, J290, J297, J298, J305, J306, J313, J314: DNP; 1X05
J5, J6, J11, J12, J19, J20, J27, J28, J35, J36, J43, J44, J51, J52, J59, J60, J67, J68, J75, J76, J83, J84, J91, J92, J99, J100, J107, J108, J115, J116, J123, J124, J131, J132, J139, J140, J147, J148, J155, J156, J163, J164, J171, J172, J179, J180, J187, J188, J195, J196, J203, J204, J211, J212, J219, J220, J227, J228, J235, J236, J243, J244, J251, J252, J259, J260, J267, J268, J275, J276, J283, J284, J291, J292, J299, J300, J307, J308, J315, J316: DNP; 1X02@1
J7, J16, J24, J32, J40, J48, J56, J64, J72, J80, J88, J96, J104, J112, J120, J128, J136, J144, J152, J160, J168, J176, J184, J192, J200, J208, J216, J224, J232, J240, J248, J256, J264, J272, J280, J288, J296, J304, J312, J320: DNP; 1X01
J8, J13, J21, J29, J37, J45, J53, J61, J69, J77, J85, J93, J101, J109, J117, J125, J133, J141, J149, J157, J165, J173, J181, J189, J197, J205, J213, J221, J229, J237, J245, J253, J261, J269, J277, J285, J293, J301, J309, J317: CORTEX_DEBUGPTH; 2X5-PTH-1.27MM
JP1, JP2, JP3, JP4, JP8, JP9, JP10, JP11, JP15, JP16, JP17, JP18, JP22, JP23, JP24, JP25, JP29, JP30, JP31, JP32, JP36, JP37, JP38, JP39, JP43, JP44, JP45, JP46, JP50, JP51, JP52, JP53, JP57, JP58, JP59, JP60, JP64, JP65, JP66, JP67, JP71, JP72, JP73, JP74, JP78, JP79, JP80, JP81, JP85, JP86, JP87, JP88, JP92, JP93, JP94, JP95, JP99, JP100, JP101, JP102, JP106, JP107, JP108, JP109, JP113, JP114, JP115, JP116, JP120, JP121, JP122, JP123, JP127, JP128, JP129, JP130, JP134, JP135, JP136, JP137, JP141, JP142, JP143, JP144, JP148, JP149, JP150, JP151, JP155, JP156, JP157, JP158, JP162, JP163, JP164, JP165, JP169, JP170, JP171, JP172, JP176, JP177, JP178, JP179, JP183, JP184, JP185, JP186, JP190, JP191, JP192, JP193, JP197, JP198, JP199, JP200, JP204, JP205, JP206, JP207, JP211, JP212, JP213, JP214, JP218, JP219, JP220, JP221, JP225, JP226, JP227, JP228, JP232, JP233, JP234, JP235, JP239, JP240, JP241, JP242, JP246, JP247, JP248, JP249, JP253, JP254, JP255, JP256, JP260, JP261, JP262, JP263, JP267, JP268, JP269, JP270, JP274, JP275, JP276, JP277: JUMPER-PAD-2; PAD-JUMPER-2-NO_YES_SILK
JP5, JP13, JP20, JP27, JP34, JP41, JP48, JP55, JP62, JP69, JP76, JP83, JP90, JP97, JP104, JP111, JP118, JP125, JP132, JP139, JP146, JP153, JP160, JP167, JP174, JP181, JP188, JP195, JP202, JP209, JP216, JP223, JP230, JP237, JP244, JP251, JP258, JP265, JP272, JP279: JUMPER-PAD-2; PAD-JUMPER-2-NC_BY_PASTE_YES_SILK
JP6, JP7, JP12, JP14, JP19, JP21, JP26, JP28, JP33, JP35, JP40, JP42, JP47, JP49, JP54, JP56, JP61, JP63, JP68, JP70, JP75, JP77, JP82, JP84, JP89, JP91, JP96, JP98, JP103, JP105, JP110, JP112, JP117, JP119, JP124, JP126, JP131, JP133, JP138, JP140, JP145, JP147, JP152, JP154, JP159, JP161, JP166, JP168, JP173, JP175, JP180, JP182, JP187, JP189, JP194, JP196, JP201, JP203, JP208, JP210, JP215, JP217, JP222, JP224, JP229, JP231, JP236, JP238, JP243, JP245, JP250, JP252, JP257, JP259, JP264, JP266, JP271, JP273, JP278, JP280: JUMPER-PAD-3-NOYES_SILK; PAD-JUMPER-3-NO_YES_SILK
LOGO1, LOGO4, LOGO7, LOGO10, LOGO13, LOGO16, LOGO19, LOGO22, LOGO25, LOGO28, LOGO31, LOGO34, LOGO37, LOGO40, LOGO43, LOGO46, LOGO49, LOGO52, LOGO55, LOGO58, LOGO61, LOGO64, LOGO67, LOGO70, LOGO73, LOGO76, LOGO79, LOGO82, LOGO85, LOGO88, LOGO91, LOGO94, LOGO97, LOGO100, LOGO103, LOGO106, LOGO109, LOGO112, LOGO115, LOGO118: SFE_LOGO_FLAME.1_INCH; SFE_LOGO_FLAME_.1
LOGO2, LOGO5, LOGO8, LOGO11, LOGO14, LOGO17, LOGO20, LOGO23, LOGO26, LOGO29, LOGO32, LOGO35, LOGO38, LOGO41, LOGO44, LOGO47, LOGO50, LOGO53, LOGO56, LOGO59, LOGO62, LOGO65, LOGO68, LOGO71, LOGO74, LOGO77, LOGO80, LOGO83, LOGO86, LOGO89, LOGO92, LOGO95, LOGO98, LOGO101, LOGO104, LOGO107, LOGO110, LOGO113, LOGO116, LOGO119: OSHW-LOGOMINI; OSHW-LOGO-MINI
LOGO3, LOGO6, LOGO9, LOGO12, LOGO15, LOGO18, LOGO21, LOGO24, LOGO27, LOGO30, LOGO33, LOGO36, LOGO39, LOGO42, LOGO45, LOGO48, LOGO51, LOGO54, LOGO57, LOGO60, LOGO63, LOGO66, LOGO69, LOGO72, LOGO75, LOGO78, LOGO81, LOGO84, LOGO87, LOGO90, LOGO93, LOGO96, LOGO99, LOGO102, LOGO105, LOGO108, LOGO111, LOGO114, LOGO117, LOGO120: SFE_LOGO_NAME_FLAME.1_INCH; SFE_LOGO_NAME_FLAME_.1
R1, R2, R9, R10, R17, R18, R25, R26, R33, R34, R41, R42, R49, R50, R57, R58, R65, R66, R73, R74, R81, R82, R89, R90, R97, R98, R105, R106, R113, R114, R121, R122, R129, R130, R137, R138, R145, R146, R153, R154, R161, R162, R169, R170, R177, R178, R185, R186, R193, R194, R201, R202, R209, R210, R217, R218, R225, R226, R233, R234, R241, R242, R249, R250, R257, R258, R265, R266, R273, R274, R281, R282, R289, R290, R297, R298, R305, R306, R313, R314: 1; 0603
R3, R4, R5, R7, R8, R11, R12, R13, R15, R16, R19, R20, R21, R23, R24, R27, R28, R29, R31, R32, R35, R36, R37, R39, R40, R43, R44, R45, R47, R48, R51, R52, R53, R55, R56, R59, R60, R61, R63, R64, R67, R68, R69, R71, R72, R75, R76, R77, R79, R80, R83, R84, R85, R87, R88, R91, R92, R93, R95, R96, R99, R100, R101, R103, R104, R107, R108, R109, R111, R112, R115, R116, R117, R119, R120, R123, R124, R125, R127, R128, R131, R132, R133, R135, R136, R139, R140, R141, R143, R144, R147, R148, R149, R151, R152, R155, R156, R157, R159, R160, R163, R164, R165, R167, R168, R171, R172, R173, R175, R176, R179, R180, R181, R183, R184, R187, R188, R189, R191, R192, R195, R196, R197, R199, R200, R203, R204, R205, R207, R208, R211, R212, R213, R215, R216, R219, R220, R221, R223, R224, R227, R228, R229, R231, R232, R235, R236, R237, R239, R240, R243, R244, R245, R247, R248, R251, R252, R253, R255, R256, R259, R260, R261, R263, R264, R267, R268, R269, R271, R272, R275, R276, R277, R279, R280, R283, R284, R285, R287, R288, R291, R292, R293, R295, R296, R299, R300, R301, R303, R304, R307, R308, R309, R311, R312, R315, R316, R317, R319, R320: 4.7k; 0603
R6, R14, R22, R30, R38, R46, R54, R62, R70, R78, R86, R94, R102, R110, R118, R126, R134, R142, R150, R158, R166, R174, R182, R190, R198, R206, R214, R222, R230, R238, R246, R254, R262, R270, R278, R286, R294, R302, R310, R318: 470; 0603
U1, U3, U5, U7, U9, U11, U13, U15, U17, U19, U21, U23, U25, U27, U29, U31, U33, U35, U37, U39, U41, U43, U45, U47, U49, U51, U53, U55, U57, U59, U61, U63, U65, U67, U69, U71, U73, U75, U77, U79: CY8C4245LQI-483; QFN-40
U2, U4, U6, U8, U10, U12, U14, U16, U18, U20, U22, U24, U26, U28, U30, U32, U34, U36, U38, U40, U42, U44, U46, U48, U50, U52, U54, U56, U58, U60, U62, U64, U66, U68, U70, U72, U74, U76, U78, U80: DRV8835; WSON-12
U$1, U$2, U$3, U$4, U$5, U$6, U$7, U$8, U$9, U$10, U$11, U$12, U$13, U$14, U$15, U$16, U$17, U$18, U$19, U$20, U$21, U$22, U$23, U$24, U$25, U$26, U$27, U$28, U$29, U$30, U$31, U$32, U$33, U$34, U$35, U$36, U$37, U$38, U$39, U$40: SPX3819M5_3_3; SOT-23-5-VREG

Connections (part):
!RESET: C7.1, J8.10, U1.30
!RESET1: C19.1, J13.10, U3.30
!RESET2: C31.1, J21.10, U5.30
!RESET3: C43.1, J29.10, U7.30
!RESET4: C55.1, J37.10, U9.30
!RESET5: C67.1, J45.10, U11.30
!RESET6: C79.1, J53.10, U13.30
!RESET7: C91.1, J61.10, U15.30
!RESET8: C103.1, J69.10, U17.30
!RESET9: C115.1, J77.10, U19.30
!RESET10: C127.1, J85.10, U21.30
!RESET11: C139.1, J93.10, U23.30
!RESET12: C151.1, J101.10, U25.30
!RESET13: C163.1, J109.10, U27.30
!RESET14: C175.1, J117.10, U29.30
!RESET15: C187.1, J125.10, U31.30
!RESET16: C199.1, J133.10, U33.30
!RESET17: C211.1, J141.10, U35.30
!RESET18: C223.1, J149.10, U37.30
!RESET19: C235.1, J157.10, U39.30
!RESET20: C247.1, J165.10, U41.30
!RESET21: C259.1, J173.10, U43.30
!RESET22: C271.1, J181.10, U45.30
!RESET23: C283.1, J189.10, U47.30
!RESET24: C295.1, J197.10, U49.30
!RESET25: C307.1, J205.10, U51.30
!RESET26: C319.1, J213.10, U53.30
!RESET27: C331.1, J221.10, U55.30
!RESET28: C343.1, J229.10, U57.30
!RESET29: C355.1, J237.10, U59.30
!RESET30: C367.1, J245.10, U61.30
!RESET31: C379.1, J253.10, U63.30
!RESET32: C391.1, J261.10, U65.30
!RESET33: C403.1, J269.10, U67.30
!RESET34: C415.1, J277.10, U69.30
!RESET35: C427.1, J285.10, U71.30
!RESET36: C439.1, J293.10, U73.30
!RESET37: C451.1, J301.10, U75.30
!RESET38: C463.1, J309.10, U77.30
!RESET39: C475.1, J317.10, U79.30
AOUT1: J1.1, U2.2
AOUT2: J1.2, U2.3
AOUT3: J14.1, U4.2
AOUT4: J14.2, U4.3
AOUT5: J22.1, U6.2
AOUT6: J22.2, U6.3
AOUT7: J30.1, U8.2
AOUT8: J30.2, U8.3
AOUT9: J38.1, U10.2
AOUT10: J38.2, U10.3
AOUT11: J46.1, U12.2
AOUT12: J46.2, U12.3
AOUT13: J54.1, U14.2
AOUT14: J54.2, U14.3
AOUT15: J62.1, U16.2
AOUT16: J62.2, U16.3
AOUT17: J70.1, U18.2
AOUT18: J70.2, U18.3
AOUT19: J78.1, U20.2
AOUT20: J78.2, U20.3
AOUT21: J86.1, U22.2
AOUT22: J86.2, U22.3
AOUT23: J94.1, U24.2
AOUT24: J94.2, U24.3
AOUT25: J102.1, U26.2
AOUT26: J102.2, U26.3
AOUT27: J110.1, U28.2
AOUT28: J110.2, U28.3
AOUT29: J118.1, U30.2
AOUT30: J118.2, U30.3
AOUT31: J126.1, U32.2
AOUT32: J126.2, U32.3
AOUT33: J134.1, U34.2
AOUT34: J134.2, U34.3
AOUT35: J142.1, U36.2
AOUT36: J142.2, U36.3
AOUT37: J150.1, U38.2
AOUT38: J150.2, U38.3
AOUT39: J158.1, U40.2
AOUT40: J158.2, U40.3
AOUT41: J166.1, U42.2
AOUT42: J166.2, U42.3
AOUT43: J174.1, U44.2
AOUT44: J174.2, U44.3
AOUT45: J182.1, U46.2
AOUT46: J182.2, U46.3
AOUT47: J190.1, U48.2
AOUT48: J190.2, U48.3
AOUT49: J198.1, U50.2
AOUT50: J198.2, U50.3
AOUT51: J206.1, U52.2
AOUT52: J206.2, U52.3
AOUT53: J214.1, U54.2
AOUT54: J214.2, U54.3
AOUT55: J222.1, U56.2
AOUT56: J222.2, U56.3
AOUT57: J230.1, U58.2
AOUT58: J230.2, U58.3
AOUT59: J238.1, U60.2
AOUT60: J238.2, U60.3
AOUT61: J246.1, U62.2
AOUT62: J246.2, U62.3
AOUT63: J254.1, U64.2
AOUT64: J254.2, U64.3
AOUT65: J262.1, U66.2
AOUT66: J262.2, U66.3
AOUT67: J270.1, U68.2
AOUT68: J270.2, U68.3
AOUT69: J278.1, U70.2
AOUT70: J278.2, U70.3
AOUT71: J286.1, U72.2
AOUT72: J286.2, U72.3
AOUT73: J294.1, U74.2
AOUT74: J294.2, U74.3
AOUT75: J302.1, U76.2
AOUT76: J302.2, U76.3
AOUT77: J310.1, U78.2
AOUT78: J310.2, U78.3
AOUT79: J318.1, U80.2
AOUT80: J318.2, U80.3
BOUT1: J3.1, U2.4
BOUT2: J3.2, U2.5
BOUT3: J15.1, U4.4
BOUT4: J15.2, U4.5
BOUT5: J23.1, U6.4
BOUT6: J23.2, U6.5
BOUT7: J31.1, U8.4
BOUT8: J31.2, U8.5
BOUT9: J39.1, U10.4
BOUT10: J39.2, U10.5
BOUT11: J47.1, U12.4
BOUT12: J47.2, U12.5
BOUT13: J55.1, U14.4
BOUT14: J55.2, U14.5
BOUT15: J63.1, U16.4
BOUT16: J63.2, U16.5
BOUT17: J71.1, U18.4
BOUT18: J71.2, U18.5
BOUT19: J79.1, U20.4
BOUT20: J79.2, U20.5
BOUT21: J87.1, U22.4
BOUT22: J87.2, U22.5
BOUT23: J95.1, U24.4
BOUT24: J95.2, U24.5
BOUT25: J103.1, U26.4
BOUT26: J103.2, U26.5
BOUT27: J111.1, U28.4
BOUT28: J111.2, U28.5
BOUT29: J119.1, U30.4
BOUT30: J119.2, U30.5
BOUT31: J127.1, U32.4
BOUT32: J127.2, U32.5
BOUT33: J135.1, U34.4
BOUT34: J135.2, U34.5
BOUT35: J143.1, U36.4
BOUT36: J143.2, U36.5
BOUT37: J151.1, U38.4
BOUT38: J151.2, U38.5
BOUT39: J159.1, U40.4
BOUT40: J159.2, U40.5
BOUT41: J167.1, U42.4
BOUT42: J167.2, U42.5
BOUT43: J175.1, U44.4
BOUT44: J175.2, U44.5
BOUT45: J183.1, U46.4
BOUT46: J183.2, U46.5
BOUT47: J191.1, U48.4
BOUT48: J191.2, U48.5
BOUT49: J199.1, U50.4
BOUT50: J199.2, U50.5
BOUT51: J207.1, U52.4
BOUT52: J207.2, U52.5
BOUT53: J215.1, U54.4
BOUT54: J215.2, U54.5
BOUT55: J223.1, U56.4
BOUT56: J223.2, U56.5
BOUT57: J231.1, U58.4
BOUT58: J231.2, U58.5
BOUT59: J239.1, U60.4
BOUT60: J239.2, U60.5
BOUT61: J247.1, U62.4
BOUT62: J247.2, U62.5
BOUT63: J255.1, U64.4
BOUT64: J255.2, U64.5
BOUT65: J263.1, U66.4
BOUT66: J263.2, U66.5
BOUT67: J271.1, U68.4
BOUT68: J271.2, U68.5
BOUT69: J279.1, U70.4
BOUT70: J279.2, U70.5
BOUT71: J287.1, U72.4
BOUT72: J287.2, U72.5
BOUT73: J295.1, U74.4
BOUT74: J295.2, U74.5
BOUT75: J303.1, U76.4
BOUT76: J303.2, U76.5
BOUT77: J311.1, U78.4
BOUT78: J311.2, U78.5
BOUT79: J319.1, U80.4
BOUT80: J319.2, U80.5
CLK_IN: J2.4, U1.28
CLK_IN1: J9.4, U3.28
CLK_IN2: J17.4, U5.28
CLK_IN3: J25.4, U7.28
CLK_IN4: J33.4, U9.28
CLK_IN5: J41.4, U11.28
CLK_IN6: J49.4, U13.28
CLK_IN7: J57.4, U15.28
CLK_IN8: J65.4, U17.28
CLK_IN9: J73.4, U19.28
CLK_IN10: J81.4, U21.28
CLK_IN11: J89.4, U23.28
CLK_IN12: J97.4, U25.28
CLK_IN13: J105.4, U27.28
CLK_IN14: J113.4, U29.28
CLK_IN15: J121.4, U31.28
CLK_IN16: J129.4, U33.28
CLK_IN17: J137.4, U35.28
CLK_IN18: J145.4, U37.28
CLK_IN19: J153.4, U39.28
CLK_IN20: J161.4, U41.28
CLK_IN21: J169.4, U43.28
CLK_IN22: J177.4, U45.28
CLK_IN23: J185.4, U47.28
CLK_IN24: J193.4, U49.28
CLK_IN25: J201.4, U51.28
CLK_IN26: J209.4, U53.28
CLK_IN27: J217.4, U55.28
CLK_IN28: J225.4, U57.28
CLK_IN29: J233.4, U59.28
CLK_IN30: J241.4, U61.28
CLK_IN31: J249.4, U63.28
CLK_IN32: J257.4, U65.28
CLK_IN33: J265.4, U67.28
CLK_IN34: J273.4, U69.28
CLK_IN35: J281.4, U71.28
CLK_IN36: J289.4, U73.28
CLK_IN37: J297.4, U75.28
CLK_IN38: J305.4, U77.28
CLK_IN39: J313.4, U79.28
CONFIG_IN: J4.4, U1.11
CONFIG_IN1: J10.4, U3.11
CONFIG_IN2: J18.4, U5.11
CONFIG_IN3: J26.4, U7.11
CONFIG_IN4: J34.4, U9.11
CONFIG_IN5: J42.4, U11.11
CONFIG_IN6: J50.4, U13.11
CONFIG_IN7: J58.4, U15.11
CONFIG_IN8: J66.4, U17.11
CONFIG_IN9: J74.4, U19.11
CONFIG_IN10: J82.4, U21.11
CONFIG_IN11: J90.4, U23.11
CONFIG_IN12: J98.4, U25.11
CONFIG_IN13: J106.4, U27.11
CONFIG_IN14: J114.4, U29.11
CONFIG_IN15: J122.4, U31.11
CONFIG_IN16: J130.4, U33.11
CONFIG_IN17: J138.4, U35.11
CONFIG_IN18: J146.4, U37.11
CONFIG_IN19: J154.4, U39.11
CONFIG_IN20: J162.4, U41.11
CONFIG_IN21: J170.4, U43.11
CONFIG_IN22: J178.4, U45.11
CONFIG_IN23: J186.4, U47.11
CONFIG_IN24: J194.4, U49.11
CONFIG_IN25: J202.4, U51.11
CONFIG_IN26: J210.4, U53.11
CONFIG_IN27: J218.4, U55.11
CONFIG_IN28: J226.4, U57.11
CONFIG_IN29: J234.4, U59.11
CONFIG_IN30: J242.4, U61.11
CONFIG_IN31: J250.4, U63.11
CONFIG_IN32: J258.4, U65.11
CONFIG_IN33: J266.4, U67.11
CONFIG_IN34: J274.4, U69.11
CONFIG_IN35: J282.4, U71.11
CONFIG_IN36: J290.4, U73.11
CONFIG_IN37: J298.4, U75.11
CONFIG_IN38: J306.4, U77.11
CONFIG_IN39: J314.4, U79.11
CONFIG_OUT: J4.5, R3.1, U1.10
CONFIG_OUT1: J10.5, R11.1, U3.10
CONFIG_OUT2: J18.5, R19.1, U5.10
CONFIG_OUT3: J26.5, R27.1, U7.10
CONFIG_OUT4: J34.5, R35.1, U9.10
CONFIG_OUT5: J42.5, R43.1, U11.10
CONFIG_OUT6: J50.5, R51.1, U13.10
CONFIG_OUT7: J58.5, R59.1, U15.10
CONFIG_OUT8: J66.5, R67.1, U17.10
CONFIG_OUT9: J74.5, R75.1, U19.10
CONFIG_OUT10: J82.5, R83.1, U21.10
CONFIG_OUT11: J90.5, R91.1, U23.10
CONFIG_OUT12: J98.5, R99.1, U25.10
CONFIG_OUT13: J106.5, R107.1, U27.10
CONFIG_OUT14: J114.5, R115.1, U29.10
CONFIG_OUT15: J122.5, R123.1, U31.10
CONFIG_OUT16: J130.5, R131.1, U33.10
CONFIG_OUT17: J138.5, R139.1, U35.10
CONFIG_OUT18: J146.5, R147.1, U37.10
CONFIG_OUT19: J154.5, R155.1, U39.10
CONFIG_OUT20: J162.5, R163.1, U41.10
CONFIG_OUT21: J170.5, R171.1, U43.10
CONFIG_OUT22: J178.5, R179.1, U45.10
CONFIG_OUT23: J186.5, R187.1, U47.10
CONFIG_OUT24: J194.5, R195.1, U49.10
CONFIG_OUT25: J202.5, R203.1, U51.10
CONFIG_OUT26: J210.5, R211.1, U53.10
CONFIG_OUT27: J218.5, R219.1, U55.10
CONFIG_OUT28: J226.5, R227.1, U57.10
CONFIG_OUT29: J234.5, R235.1, U59.10
CONFIG_OUT30: J242.5, R243.1, U61.10
CONFIG_OUT31: J250.5, R251.1, U63.10
CONFIG_OUT32: J258.5, R259.1, U65.10
CONFIG_OUT33: J266.5, R267.1, U67.10
CONFIG_OUT34: J274.5, R275.1, U69.10
CONFIG_OUT35: J282.5, R283.1, U71.10
CONFIG_OUT36: J290.5, R291.1, U73.10
CONFIG_OUT37: J298.5, R299.1, U75.10
CONFIG_OUT38: J306.5, R307.1, U77.10
CONFIG_OUT39: J314.5, R315.1, U79.10
GND: C1.2, C2.2, C3.2, C4.2, C5.2, C6.2, C7.2, C8.2, C9.2, C10.-, C11.2, C12.-, D1.C, J2.3, J4.1, J6.1, J6.2, J8.3, J8.5, J8.7, J8.9, JP1.1, JP2.1, JP3.1, JP4.1, R3.2, U1.9, U1.34, U1.EP, U2.6, U2.PAD, U$3.2
GND1: C13.2, C14.2, C15.2, C16.2, C17.2, C18.2, C19.2, C20.2, C21.2, C22.-, C23.2, C24.-, D2.C, J9.3, J10.1, J12.1, J12.2, J13.3, J13.5, J13.7, J13.9, JP8.1, JP9.1, JP10.1, JP11.1, R11.2, U3.9, U3.34, U3.EP, U4.6, U4.PAD, U$1.2
GND2: C25.2, C26.2, C27.2, C28.2, C29.2, C30.2, C31.2, C32.2, C33.2, C34.-, C35.2, C36.-, D3.C, J17.3, J18.1, J20.1, J20.2, J21.3, J21.5, J21.7, J21.9, JP15.1, JP16.1, JP17.1, JP18.1, R19.2, U5.9, U5.34, U5.EP, U6.6, U6.PAD, U$2.2
GND3: C37.2, C38.2, C39.2, C40.2, C41.2, C42.2, C43.2, C44.2, C45.2, C46.-, C47.2, C48.-, D4.C, J25.3, J26.1, J28.1, J28.2, J29.3, J29.5, J29.7, J29.9, JP22.1, JP23.1, JP24.1, JP25.1, R27.2, U7.9, U7.34, U7.EP, U8.6, U8.PAD, U$4.2
GND4: C49.2, C50.2, C51.2, C52.2, C53.2, C54.2, C55.2, C56.2, C57.2, C58.-, C59.2, C60.-, D5.C, J33.3, J34.1, J36.1, J36.2, J37.3, J37.5, J37.7, J37.9, JP29.1, JP30.1, JP31.1, JP32.1, R35.2, U9.9, U9.34, U9.EP, U10.6, U10.PAD, U$5.2
GND5: C61.2, C62.2, C63.2, C64.2, C65.2, C66.2, C67.2, C68.2, C69.2, C70.-, C71.2, C72.-, D6.C, J41.3, J42.1, J44.1, J44.2, J45.3, J45.5, J45.7, J45.9, JP36.1, JP37.1, JP38.1, JP39.1, R43.2, U11.9, U11.34, U11.EP, U12.6, U12.PAD, U$6.2
GND6: C73.2, C74.2, C75.2, C76.2, C77.2, C78.2, C79.2, C80.2, C81.2, C82.-, C83.2, C84.-, D7.C, J49.3, J50.1, J52.1, J52.2, J53.3, J53.5, J53.7, J53.9, JP43.1, JP44.1, JP45.1, JP46.1, R51.2, U13.9, U13.34, U13.EP, U14.6, U14.PAD, U$7.2
GND7: C85.2, C86.2, C87.2, C88.2, C89.2, C90.2, C91.2, C92.2, C93.2, C94.-, C95.2, C96.-, D8.C, J57.3, J58.1, J60.1, J60.2, J61.3, J61.5, J61.7, J61.9, JP50.1, JP51.1, JP52.1, JP53.1, R59.2, U15.9, U15.34, U15.EP, U16.6, U16.PAD, U$8.2
GND8: C97.2, C98.2, C99.2, C100.2, C101.2, C102.2, C103.2, C104.2, C105.2, C106.-, C107.2, C108.-, D9.C, J65.3, J66.1, J68.1, J68.2, J69.3, J69.5, J69.7, J69.9, JP57.1, JP58.1, JP59.1, JP60.1, R67.2, U17.9, U17.34, U17.EP, U18.6, U18.PAD, U$9.2
GND9: C109.2, C110.2, C111.2, C112.2, C113.2, C114.2, C115.2, C116.2, C117.2, C118.-, C119.2, C120.-, D10.C, J73.3, J74.1, J76.1, J76.2, J77.3, J77.5, J77.7, J77.9, JP64.1, JP65.1, JP66.1, JP67.1, R75.2, U19.9, U19.34, U19.EP, U20.6, U20.PAD, U$10.2
GND10: C121.2, C122.2, C123.2, C124.2, C125.2, C126.2, C127.2, C128.2, C129.2, C130.-, C131.2, C132.-, D11.C, J81.3, J82.1, J84.1, J84.2, J85.3, J85.5, J85.7, J85.9, JP71.1, JP72.1, JP73.1, JP74.1, R83.2, U21.9, U21.34, U21.EP, U22.6, U22.PAD, U$11.2
GND11: C133.2, C134.2, C135.2, C136.2, C137.2, C138.2, C139.2, C140.2, C141.2, C142.-, C143.2, C144.-, D12.C, J89.3, J90.1, J92.1, J92.2, J93.3, J93.5, J93.7, J93.9, JP78.1, JP79.1, JP80.1, JP81.1, R91.2, U23.9, U23.34, U23.EP, U24.6, U24.PAD, U$12.2
GND12: C145.2, C146.2, C147.2, C148.2, C149.2, C150.2, C151.2, C152.2, C153.2, C154.-, C155.2, C156.-, D13.C, J97.3, J98.1, J100.1, J100.2, J101.3, J101.5, J101.7, J101.9, JP85.1, JP86.1, JP87.1, JP88.1, R99.2, U25.9, U25.34, U25.EP, U26.6, U26.PAD, U$13.2
GND13: C157.2, C158.2, C159.2, C160.2, C161.2, C162.2, C163.2, C164.2, C165.2, C166.-, C167.2, C168.-, D14.C, J105.3, J106.1, J108.1, J108.2, J109.3, J109.5, J109.7, J109.9, JP92.1, JP93.1, JP94.1, JP95.1, R107.2, U27.9, U27.34, U27.EP, U28.6, U28.PAD, U$14.2
GND14: C169.2, C170.2, C171.2, C172.2, C173.2, C174.2, C175.2, C176.2, C177.2, C178.-, C179.2, C180.-, D15.C, J113.3, J114.1, J116.1, J116.2, J117.3, J117.5, J117.7, J117.9, JP99.1, JP100.1, JP101.1, JP102.1, R115.2, U29.9, U29.34, U29.EP, U30.6, U30.PAD, U$15.2
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

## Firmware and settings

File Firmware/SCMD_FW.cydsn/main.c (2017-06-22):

/******************************************************************************
main.c
Serial controlled motor driver firmware
marshall.taylor@sparkfun.com
7-8-2016
https://github.com/sparkfun/Serial_Controlled_Motor_Driver/

See github readme for mor information.

This code is released under the [MIT License](http://opensource.org/licenses/MIT).
Please review the LICENSE.md file included with this example. If you have any questions
or concerns with licensing, please contact techsupport@sparkfun.com.
Distributed as-is; no warranty is given.
******************************************************************************/
#include <project.h>
#include "devRegisters.h"
#include "charMath.h"
#include "SCMD_config.h"
#include "serial.h"
#include "diagLEDS.h"
#include "slaveEnumeration.h"
#include "customSerialInterrupts.h"
#include "registerHandlers.h"

//Debug stuff
//If USE_SW_CONFIG_BITS is defined, program will use CONFIG_BITS instead of the solder jumpers on the board:
//#define USE_SW_CONFIG_BITS

//Otherwise, this global is used to get the bits from the hardware jumpers.
//Valid options:
//  0x0         -- UART
//  0x1         -- SPI
//  0x2         -- I2C slave on slave port
//  0x3 to 0xE  -- I2C @ 0x58 to 0x63
//  0xF         -- PWM mode (not implemented)
volatile uint8_t CONFIG_BITS = 0x0;

//Prototypes
static void systemInit( void ); //get the system off the ground - calls warm init - run once at start

//Variables for use with timer ISR to measure time. 
volatile uint16_t masterSendCounter = 65000;
volatile bool masterSendCounterReset = 0;
volatile bool breakCounterWait = false;

//Reboot variable
extern volatile bool slaveResetRequested;

//Functions
int main()
{
    systemInit();

    while(1)
    {
		DEBUG_TIMER_Stop();
		DEBUG_TIMER_WriteCounter(0);
		DEBUG_TIMER_Start();
		
        if((CONFIG_BITS == 0) || (CONFIG_BITS == 0x0D) || (CONFIG_BITS == 0x0E)) //UART
        {
            parseUART();
        }
        else if((CONFIG_BITS >= 0x3)&&(CONFIG_BITS <= 0xC)) //I2C
        {
            //parceI2C is also called before interrupts occur on the bus, but check here too to catch residual buffers
            parseI2C();
        }
        //parseSPI() now called from within the interrupt only

       
        if(CONFIG_BITS == 2) //Slave
        {
            parseSlaveI2C();
            tickSlaveSM();
            processSlaveRegChanges();
        }
        else //Do master operations
        {
			tickMasterSM();
            processMasterRegChanges();

        }        
        //operations regardless       
        processRegChanges();
        
		//Save time
		uint32_t tempValue = DEBUG_TIMER_ReadCounter() / 100;
		if(tempValue > 0xFF) tempValue = 0xFF;
		//do 'peak hold' on SCMD_UPORT_TIME -- write 0 to reset
		if(tempValue > readDevRegister(SCMD_LOOP_TIME)) writeDevRegister(SCMD_LOOP_TIME, tempValue);
    }//End of while loop
}

/*******************************************************************************
* Define Interrupt service routine and allocate an vector to the Interrupt
********************************************************************************/
CY_ISR(FSAFE_TIMER_Interrupt)
{
    CyGlobalIntDisable;
    /* Clear TC Inerrupt */
   	FSAFE_TIMER_ClearInterrupt(FSAFE_TIMER_INTR_MASK_CC_MATCH);
    incrementDevRegister( SCMD_FSAFE_FAULTS );
    
    //  Plan to escape counter wait
    breakCounterWait = true;
    
    //  Collect behavior information
    uint8_t drive_behavior = readDevRegister(SCMD_FSAFE_CTRL) & SCMD_FSAFE_DRIVE_KILL;
    uint8_t reset_behavior = (readDevRegister(SCMD_FSAFE_CTRL) & SCMD_FSAFE_RESTART_MASK) >> 1;
    uint8_t user_behavior = (readDevRegister(SCMD_FSAFE_CTRL) & SCMD_FSAFE_CYCLE_USER) >> 3;
    uint8_t expansion_behavior = (readDevRegister(SCMD_FSAFE_CTRL) & SCMD_FSAFE_CYCLE_EXP) >> 4;
    
    //  Stop the motor
    if( drive_behavior == 1)
    {
        writeDevRegister( SCMD_MA_DRIVE, 0x80 );
        writeDevRegister( SCMD_MB_DRIVE, 0x80 );
    }
	//  Restart user or expansion ports
    if( user_behavior == 1)
    {
        initUserSerial(CONFIG_BITS);
    }
    if( expansion_behavior == 1)
    {
        initExpansionSerial(CONFIG_BITS); 
    }
    //  Re-enumerate or reboot
    switch(reset_behavior)
    {
        default:
        case 0x00:
        break;
        case 0x01: //Reboot
            hardReset();
        break;
        case 0x02: //Re-enumerate
            reEnumerate();
        break;
    }
    
    //  Tell someone
    setDiagMessage(7,8);
    
    //  reset the counter
    FSAFE_TIMER_Stop();
    FSAFE_TIMER_WriteCounter(0);
    FSAFE_TIMER_Start();
    CyGlobalIntEnable;

}

/*******************************************************************************
* Define Interrupt service routine and allocate an vector to the Interrupt
********************************************************************************/
CY_ISR(ConfigInBehaviorHandler)
{
    CyGlobalIntDisable;
    M_IN_ISR_Stop();
    CONFIG_IN_ClearInterrupt();
   
    //Send the reset request
    switch( readDevRegister( SCMD_MST_E_IN_FN ) & SCMD_M_IN_RESTART_MASK )
    {
        default:
        case 0:
            //  Restart user or expansion ports
            if(readDevRegister( SCMD_MST_E_IN_FN ) & SCMD_M_IN_CYCLE_USER )
            {
                initUserSerial( readDevRegister( SCMD_CONFIG_BITS ) );
                CyDelay(100);
            }
            if(readDevRegister( SCMD_MST_E_IN_FN ) & SCMD_M_IN_CYCLE_EXP )
            {
                initExpansionSerial( readDevRegister( SCMD_CONFIG_BITS ) );
                CyDelay(100);
            }
            M_IN_ISR_StartEx(ConfigInBehaviorHandler);
        break;
        case 1:
            hardReset();
        break;
        case 2:
            //  Restart user or expansion ports
            if(readDevRegister( SCMD_MST_E_IN_FN ) & SCMD_M_IN_CYCLE_USER )
            {
                initUserSerial( readDevRegister( SCMD_CONFIG_BITS ) );
                CyDelay(100);
            }
            if(readDevRegister( SCMD_MST_E_IN_FN ) & SCMD_M_IN_CYCLE_EXP )
            {
                initExpansionSerial( readDevRegister( SCMD_CONFIG_BITS ) );
                CyDelay(100);
            }
            writeDevRegister( SCMD_CONTROL_1, readDevRegister( SCMD_CONTROL_1 ) | SCMD_RE_ENUMERATE_BIT ); //Set bit
            M_IN_ISR_StartEx(ConfigInBehaviorHandler);
        break;
    }
    
    CyGlobalIntEnable;

}

/* ISR prototype declaration */
CY_ISR_PROTO(SYSTICK_ISR);

/* User ISR function definition */
CY_ISR(SYSTICK_ISR)
{
	/* User ISR Code*/
    if(masterSendCounterReset)
    {
        //clear reset
        masterSendCounterReset = 0;
        masterSendCounter = 0;
    }
    else
    {
        if(masterSendCounter < 0xFFFF) //hang at top value
        {
            masterSendCounter++;
        }
    }
}

//get the system off the ground - run once at start
static void systemInit( void )
{
    initDevRegisters();  //Prep device registers, set initial values (triggers actions)
#ifndef USE_SW_CONFIG_BITS
    CONFIG_BITS = readDevRegister(SCMD_CONFIG_BITS); //Get the bits value
#endif
    
    DIAG_LED_CLK_Stop();
    DIAG_LED_CLK_Start();
    KHZ_CLK_Stop();
    KHZ_CLK_Start();
    //setDiagMessage(0, CONFIG_BITS);
    
    CONFIG_IN_Write(0); //Tell the slaves to start fresh
    //Do a boot-up delay
    CyDelay(100u);
    if(CONFIG_BITS != 0x02) CyDelay(1000u); //Give the slaves extra time
    
    MODE_Write(1);
    
    //Debug timer
    DEBUG_CLK_Stop();
    DEBUG_CLK_Start();
    DEBUG_TIMER_Stop();
    DEBUG_TIMER_Start();
    
    //SysTick timer (software driven)
    // Map systick ISR to the user defined ISR. SysTick_IRQn is already defined in core_cm0.h file
	CyIntSetSysVector((SysTick_IRQn + 16), SYSTICK_ISR);
	
    /* Enable Systick timer with desired period/number of ticks */
	SysTick_Config(24000);  //Interrupt should occur every 1 ms
    
    //Failsafe timer
    FSAFE_ISR_StartEx(FSAFE_TIMER_Interrupt);
    FSAFE_CLK_Stop();
    FSAFE_CLK_Start();
    FSAFE_TIMER_Stop();
    FSAFE_TIMER_Start();
       
    CyDelay(50u);
    
    /* Start the components */
    PWM_1_Start();
    PWM_1_WriteCompare(128u);
    PWM_2_Start();
    PWM_2_WriteCompare(128u);        
    
    //This configures the serial based on the config structures in serial.h
    //It connects the functions in customSerialInterrupts.h, and is defined in that file.
	calcUserDivider(CONFIG_BITS);
	calcExpansionDivider(CONFIG_BITS);

    initUserSerial(CONFIG_BITS);
	initExpansionSerial(CONFIG_BITS);
    
    //Clock_1 is the motor PWM clock
    Clock_1_Stop();
    Clock_1_Start();
    
    //Config in behavior
    if(CONFIG_BITS != 0x02) M_IN_ISR_StartEx(ConfigInBehaviorHandler);
    
    CyGlobalIntEnable; 
    
    setDiagMessage(1, 1);

}

/* [] END OF FILE */

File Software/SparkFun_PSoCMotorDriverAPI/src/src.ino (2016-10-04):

//This example sends knob inputs out to motors 1, 2, 3, 4 via I2C
//It returns diagnostic information



//HOW TO OPERATE
//  Make TimerClass objects for each thing that needs periodic service
//  pass the interval of the period in ticks
//
//  Set maxInterval to rollover rate
//  Set maxTimer to the max foreseen interval of any timer.
//  maxTimer + maxInterval = max countable value.
#include "HOS_char.h"
#include "SerialControlledMotorDriverAPI.h"
#include "config.h"

//Globals
uint16_t maxTimer = 60000;
uint16_t maxInterval = 2000;

#define LEDPIN 13
#include "timerModule.h"
#include "stdint.h"

//Not used by this sketch but dependant on one 
#include "Wire.h"

//If 328p based, do this
#ifdef __AVR__
#include <Arduino.h>
#endif

//If Teensy 3.1 based, do this
#ifdef __MK20DX256__
IntervalTimer myTimer;
#endif

//Globals
TimerClass debugTimer( 3000 ); //milliseconds between calls
TimerClass outputTimer( 50 );  //Read knobs and drive motors

//Required for timers:
uint16_t msTicks = 0;
uint8_t msTicksLocked = 1; //start locked out

SCMD myMotorDriver;

//Diagnostic
uint16_t durationRecord[1] = {0};

void setup()
{
	Serial.begin(115200);
	pinMode(LEDPIN, OUTPUT);

	pinMode(A0, INPUT);
	pinMode(A1, INPUT);
	pinMode(A2, INPUT);
	pinMode(A3, INPUT);
	
	pinMode(4, OUTPUT);
	digitalWrite(4, 0);
	
	delay(1500);
	Serial.println("Starting sketch.");

	//Specify configuration for the driver
	myMotorDriver.settings.commInterface = I2C_MODE;
	myMotorDriver.settings.I2CAddress = 0x5A;
	//myMotorDriver.settings.chipSelectPin = 10;
	//myMotorDriver.settings.invertA = 1;
	//myMotorDriver.settings.invertB = 1;

	Serial.println("Starting timer.");
	//If 328p based, do this -- Creates interrupt based timer
#ifdef __AVR__
	// initialize Timer1
	cli();          // disable global interrupts
	TCCR1A = 0;     // set entire TCCR1A register to 0
	TCCR1B = 0;     // same for TCCR1B

	// set compare match register to desired timer count:
	OCR1A = 16000;

	// turn on CTC mode:
	TCCR1B |= (1 << WGM12);

	// Set CS10 and CS12 bits for 1 prescaler:
	TCCR1B |= (1 << CS10);

	// enable timer compare interrupt:
	TIMSK1 |= (1 << OCIE1A);

	// enable global interrupts:
	sei();
#endif

	//If Teensy 3.1 based, do this
#ifdef __MK20DX256__
	// initialize IntervalTimer
	myTimer.begin(serviceMS, 1000);  // serviceMS to run every 0.001 seconds
#endif
	
	Serial.print("Starting driver... ID = 0x");
	delay(500);
	digitalWrite(4, 1);
	digitalWrite(4, 0);
	digitalWrite(4, 1);
	Serial.println(myMotorDriver.begin(), HEX);
	myMotorDriver.bridgingMode(0,1);
	myMotorDriver.inversionMode(2,1);
}

void loop()
{
	//Update the timers, but only once per interrupt
	if( msTicksLocked == 0 )
	{
		//**Copy to make a new timer******************//  
		//msTimerA.update(msTicks);
		debugTimer.update(msTicks);
		outputTimer.update(msTicks);
		
		//Done?  Lock it back up
		msTicksLocked = 1;
	}  //The ISR will unlock.

	//Check the timers
	if(debugTimer.flagStatus() == PENDING)
	{
		//User code
		digitalWrite( LEDPIN, digitalRead( LEDPIN ) ^ 0x01 );
		Serial.println("\nOOoo..   Debug Interval Timer   ..ooOO");
		Serial.print("ID: 0x");
		Serial.println(myMotorDriver.readRegister(SCMD_ID), HEX);
		
		Serial.println("MEMORY DUMP:");
		for( int i = 0x17; i < 0x1A; i++)
		{
			Serial.print("0x");
			Serial.print(i, HEX);
			Serial.print(": 0x");
			Serial.println(myMotorDriver.readRegister(i), HEX);
		}		
		Serial.println("MEMORY DUMP:");
		for( int i = 0x60; i < 0x68; i++)
		{
			Serial.print("0x");
			Serial.print(i, HEX);
			Serial.print(": 0x");
			Serial.println(myMotorDriver.readRegister(i), HEX);
		}		
		Serial.print("outputTimer Fn Duration Peak: ");
		Serial.print(durationRecord[0]);
		Serial.println("ms");
		durationRecord[0] = 0;
		Serial.print("I2C routine duration: ");
		Serial.print(myMotorDriver.readRegister(SCMD_UPORT_TIME));
		Serial.println("us");
		Serial.print("I2C RX error cnt: ");
		Serial.println(myMotorDriver.readRegister(SCMD_I2C_RD_ERR));
		Serial.print("I2C WR error cnt: ");
		Serial.println(myMotorDriver.readRegister(SCMD_I2C_WR_ERR));
		//Serial.print("debug out: ");
		//Serial.println(myMotorDriver.readRegister(SCMD_MA_DRIVE));
		}
	//**Script timer******************//  
	if(outputTimer.flagStatus() == PENDING)
	{
		uint16_t timeVariable = msTicks;
		//Read inputs
		int8_t inputAnalog[4];
		
		for( int i = 0; i < 4; i++)
		{
			//Convert to -128 to 127
			inputAnalog[i] = (int16_t)(analogRead(i) >> 2) - 128;
		}
			
		//Send outputs
		for( int i = 0; i < 4; i++)
		{
			if(inputAnalog[i] >= 0)
			{
				myMotorDriver.setDrive(i,1,inputAnalog[i]); //Drive motor i forward
			}
			else
			{
				myMotorDriver.setDrive(i,0,inputAnalog[i] * -1); //Drive motor i backward
			}
			delay(1);
		}
		timeVariable = msTicks - timeVariable;
		if( timeVariable > durationRecord[0] )
		{
			durationRecord[0] = timeVariable;
		}
	}
}

//If 328p based, do this
#ifdef __AVR__
ISR(TIMER1_COMPA_vect)
#else
#endif
//If Teensy 3.1 based, do this
#ifdef __MK20DX256__
void serviceMS(void)
#else
#endif
{
	uint32_t returnVar = 0;
	if( msTicks >= ( maxTimer + maxInterval ) )
	{
		returnVar = msTicks - maxTimer;

	}
	else
	{
		returnVar = msTicks + 1;
	}
	msTicks = returnVar;
	msTicksLocked = 0;  //unlock
}

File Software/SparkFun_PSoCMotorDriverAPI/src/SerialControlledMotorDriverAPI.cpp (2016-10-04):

/******************************************************************************
SparkFun_PSoCMotorDriverAPI.cpp
SCMD Arduino and Teensy Driver
Marshall Taylor @ SparkFun Electronics
May 20, 2015
https://github.com/sparkfun/______________

<multiline verbose description of file functionality>

Resources:
Uses Wire.h for i2c operation
Uses SPI.h for SPI operation

Development environment specifics:
<arduino/development environment version>
<hardware version>
<etc>

This code is released under the [MIT License](http://opensource.org/licenses/MIT).

Please review the LICENSE.md file included with this example. If you have any questions 
or concerns with licensing, please contact techsupport@sparkfun.com.

Distributed as-is; no warranty is given.
******************************************************************************/
//Define USE_ALT_I2C to use the teesny 3 i2c_t3.h library, which allows I2C bus hang resolution
//#define USE_ALT_I2C

//See _____ for additional topology notes.

#include "SerialControlledMotorDriverAPI.h"
#include "stdint.h"
#include <math.h>
#include "config.h"

#ifdef USE_ALT_I2C
#include <i2c_t3.h>
#define I2C_FAULT_TIMEOUT 1000 //in microseconds
#else
#include "Wire.h"
#endif

#include "SPI.h"

//****************************************************************************//
//
//  Settings and configuration
//
//****************************************************************************//

//Constructor -- Specifies default configuration
SCMD::SCMD( void )
{
	//Construct with these default settings if nothing is specified

	//Select interface mode
	settings.commInterface = I2C_MODE; //Can be I2C_MODE, SPI_MODE
	//Select address for I2C.  Does nothing for SPI
	settings.I2CAddress = 0x58; //Ignored for SPI_MODE
	//Select CS pin for SPI.  Does nothing for I2C
	settings.chipSelectPin = 10;
	settings.invertA = 0;
	settings.invertB = 0;
	

}


//****************************************************************************//
//
//  Configuration section
//
//  This uses the stored SensorSettings to start the IMU
//  Use statements such as "mySensor.settings.commInterface = SPI_MODE;" to 
//  configure before calling .begin();
//
//****************************************************************************//
uint8_t SCMD::begin()
{
	//Check the settings structure values to determine how to setup the device
	uint8_t dataToWrite = 0;  //Temporary variable

	switch (settings.commInterface)
	{

	case I2C_MODE:
		Wire.begin(settings.I2CAddress);
		break;

	case SPI_MODE:
		// start the SPI library:
		SPI.begin();
		// Maximum SPI frequency is 10MHz, could divide by 2 here:
		SPI.setClockDivider(SPI_CLOCK_DIV32);
		// Data is read and written MSb first.
		SPI.setBitOrder(MSBFIRST);
		// Data is captured on rising edge of clock (CPHA = 0)
		// Base value of the clock is HIGH (CPOL = 1)
		// This was SPI_MODE3 for RedBoard, but I had to change to
		// MODE0 for Teensy 3.1 operation
		SPI.setDataMode(SPI_MODE3);
		// initalize the  data ready and chip select pins:
		pinMode(settings.chipSelectPin, OUTPUT);
		digitalWrite(settings.chipSelectPin, HIGH);
		break;

	default:
		break;
	}
	
	//dummy read
	readRegister(SCMD_ID);
	writeRegister(SCMD_DRIVER_ENABLE, 0x01);
	delay(10);

	return readRegister(SCMD_ID);
}

//Reset function
void SCMD::reset( void )
{
#ifdef USE_ALT_I2C
	//Blast the Teensy 3.1 i2c control register
	uint8_t * I2C_CTRL1_reg;
	I2C_CTRL1_reg = (uint8_t *)0x40066002;
	*I2C_CTRL1_reg = 0x00;
	//Waiting seems like a good idea
	delay(10);
	Wire.resetBus(); //Strictly resets.  Run .begin() afterwards
	Wire.begin();
#endif
	
}
//****************************************************************************//
//
//  Drive Section
//
//****************************************************************************//
void SCMD::setDrive( uint8_t channel, uint8_t direction, uint8_t level )
{
	//convert to 7 bit
	level = level >> 1;
	int16_t driveValue; //use to build value to actually write to register
	
	switch(channel)
	{
		case 0:  //master
			direction ^= settings.invertA;
			driveValue = (level * direction) + ((int8_t)level * ((int8_t)direction - 1)); //set to 1/2 drive if direction = 1 or -1/2 drive if direction = 0; (level * direction);
			driveValue += 128;
			writeRegister(SCMD_MA_DRIVE, driveValue);
			break;
		case 1:  //master
			direction ^= settings.invertB;
			driveValue = (level * direction) + ((int8_t)level * ((int8_t)direction - 1)); //set to 1/2 drive if direction = 1 or -1/2 drive if direction = 0; (level * direction);
			driveValue += 128;
			writeRegister(SCMD_MB_DRIVE, driveValue);
			break;
		default:
		break;
	}
}

void SCMD::inversionMode( uint8_t motorNum, uint8_t polarity )
{
	uint8_t regTemp;
	//Select target register
	if( motorNum < 2 )
	{
		//master
		if( motorNum == 0 ) writeRegister(SCMD_MOTOR_A_INVERT, polarity & 0x01);
		if( motorNum == 1 ) writeRegister(SCMD_MOTOR_B_INVERT, polarity & 0x01);
	}
	else
	{
		if( motorNum < 10 )
		{
			//register: SCMD_INV_2_9
			regTemp = SCMD_INV_2_9;
			motorNum -= 2;

		}
		else if( motorNum < 18 )
		{
			//register: SCMD_INV_10_17
			regTemp = SCMD_INV_10_17;
			motorNum -= 10;
		}
		else if( motorNum < 26 )
		{
			//register: SCMD_INV_18_25
			regTemp = SCMD_INV_18_25;
			motorNum -= 18;
		}
		else if( motorNum < 34 )
		{
			//register: SCMD_INV_26_33
			regTemp = SCMD_INV_26_33;
			motorNum -= 26;
		}
		else
		{
			//out of range
			return;
		}
		//convert motorNum to one-hot mask
		motorNum = 1 << motorNum;
		uint8_t data = readRegister( regTemp );
		//clear bit
		data &= ~motorNum;
		writeRegister( regTemp, data | (polarity & 0x01) );
	}

}

void SCMD::bridgingMode( uint8_t driverNum, uint8_t bridged )
{
	uint8_t regTemp;
	//Select target register
	if( driverNum < 1 )
	{
		//master
		writeRegister(SCMD_BRIDGE, bridged & 0x01);
	}
	else
	{
		if( driverNum < 9 )
		{
			//register: SCMD_BRIDGE_SLV_L
			regTemp = SCMD_BRIDGE_SLV_L;
			driverNum -= 1;

		}
		else if( driverNum < 17 )
		{
			//register: SCMD_BRIDGE_SLV_H
			regTemp = SCMD_BRIDGE_SLV_H;
			driverNum -= 9;
		}
		else
		{
			//out of range
			return;
		}
		//convert driverNum to one-hot mask
		driverNum = 1 << driverNum;
		uint8_t data = readRegister( regTemp );
		//clear bit
		data &= ~driverNum;
		writeRegister( regTemp, data | (bridged & 0x01) );
	}
	
}
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

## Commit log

2015-03-09 Adding hardware files, README
    [Serial_Controlled_Dual_Motor_Driver-v12.brd, Serial_Controlled_Dual_Motor_Driver-v12.sch]
2016-04-18 added new design
    [PSocC Motor Driver Design 1.brd, PSocC Motor Driver Design 1.sch, Serial_Controlled_Dual_Motor_Driver-v12.brd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]
2016-04-20 Sending it home
    [PSocC Motor Driver Design 1.brd, PSocC Motor Driver Design 1.sch]
2016-04-21 Working on checklist
    [Board_Design_Checklist.ods, PSocC Motor Driver Design 1.brd, PSocC Motor Driver Design 1.sch]
2016-04-22 Finished checklist
    [Board_Design_Checklist.ods, PSocC Motor Driver Design 1.brd, PSocC Motor Driver Design 1.sch]
2016-06-30 bringing branch up to date with physical hardware v1.5
    [PSocC Motor Driver Design 1.brd, PSocC Motor Driver Design 1.sch]
2016-06-30 Bringing branch up to date with current design work while tracking only necessary PSoC build files
    [Board_Design_Checklist.ods, RegisterMap.ods, Serial Controlled Motor Driver.brd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]
2016-07-06 Added no-driver version for development
    [Serial Controlled Module.brd, Serial Controlled Module.sch]
2016-07-15 Made non-zero widths and put tags in readme
    [Serial Controlled Module.brd, Serial Controlled Motor Driver.brd]
2016-07-15 Incremented version numbers in eagle files
    [Serial Controlled Motor Driver.brd, Serial Controlled Motor Driver.sch]
2016-07-15 Thickened poly lines to 0.001 inch
    [Serial Controlled Motor Driver.brd]
2016-07-17 Established simple API sketch to run on either Arduino UNO or Teensy 3.2
    [RegisterMap.ods]
2016-07-20 Brought 2nd proto up, fixed i2c config bug
    [devRegisters.c, main.c]
2016-07-26 Working on release FW, added status LED, config bit reading, starting to fill out the register map
    [RegisterMap.ods]
2016-07-27 Added I2C error checking, saves into register map
    [RegisterMap.ods]
2016-08-03 Snapshot of the single driver only code. All IO added, LED behaves well, driver good for driving robots. Expansion port configured to be master, and can take random data from a slave through a junky 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
    [ConfigBits.ods, RegisterMap.ods]
2016-08-04 got read and write to slave device working, though experiencing a bus lockup when there's no slave at the specified address
    [RegisterMap.ods]
2016-08-04 Now supports enumeration of slave devices. During boot, slaves are assigned an address based on when the CONFIG_IN pin goes high. Also did a bit of work on the UNO test appliance.
    [RegisterMap.ods]
2016-08-06 Added self-reboot to slaves that lose sync, added max 16 slaves, debugged
    [main.c]
2016-08-09 Fixed proto errors and started final API for arduino
    [Serial Controlled Motor Driver.brd, Serial Controlled Motor Driver.sch, TP1.ods]
2016-08-11 added test docs
    [TP2.ods]
2016-08-11 Added Byron's review suggestions
    [Serial Controlled Motor Driver.brd, Serial Controlled Motor Driver.sch]
2016-08-12 Finished review and implemented changes, double checked serial pin functions to match silk
    [Serial Controlled Module.brd, Serial Controlled Module.sch, Serial Controlled Motor Driver.brd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]
2016-08-16 Paneling of board
    Board Panel reviewed with Marshall.
    [Serial Controlled Motor Driver-panel_v20.brd]
2016-08-16 Fixed naming
    Fixed naming forgot pcb #
    [13346-Serial Controlled Motor Driver-panel_v20.brd]
2016-09-26 Added uart parser and documentation
2016-09-27 Implemented arbitrary uart RW and polarity/bridging mux
    [RegisterMap.ods]
2016-09-29 Alpha release of firmware. All functions implemented but require testing and debugging.
    [RegisterMap.ods]
2016-10-02 Added documentation and condensed UART parsing code
2016-10-03 Fixed headers, cleaned up a bit
    [devRegisters.c, diagLEDs.c, main.c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]
2016-10-04 Purged examples, writing arduino library
    [RegisterMap.ods]
2016-10-12 Major reworking of FW and SW complete. I2C and SPI work through the Arduino library. I2C, SPI, UART, and slave operation works in the FW, very near to as expected.
    [RegisterMap.ods]
2016-10-16 added diag, timeout, refined failsafe, wrote diag example
    [RegisterMap.ods]
2016-10-17 Created new files, and moved functions, for serial parsers and device register actions
2016-10-18 Enabled write lockouts, rearranged device registers
    [RegisterMap.ods]
2016-10-18 switched to DEBUG built fw
2016-10-19 polished functions
    [RegisterMap.ods]
2016-10-19 Started datasheet
    [RegisterMap.ods]
2016-10-20 working out serial timing
    [RegisterMap.ods]
2016-10-20 Reorganized serial. Created handlers for user and expansion bus divider registers, and broke serial init up into smaller parts.
    [customSerialInterrupts.c, devRegisters.c, main.c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]
2016-10-24 worked on documentation
    [ConfigBits.ods, DatasheetTables.ods]
2016-10-25 More documentation changes
    [DatasheetTables.ods]
2016-10-26 Documentation update
    [DatasheetTables.ods, RegisterMap.ods]
2016-10-27 Working on QC test
    [RegisterMap.ods]
2016-10-27 added some test mode stuff and removed old workspaces. Generated SCMD_FID_04.HEX
    [DatasheetTables.ods, RegisterMap.ods]
2016-10-29 Working on documentation
    [RegisterMap.ods]
2016-10-31 Tweaking operation
    [DatasheetTables.ods]
2016-10-31 Updated documentation
    [DatasheetTables.ods, redsThermal.ods]
2016-11-03 Overhauled boot order and reboot operations, added busy bit
    [RegisterMap.ods]
2016-11-03 Debugging serial parser
    [RegisterMap.ods]
2016-11-04 Added enumeration diagrams to datasheet
    [DatasheetTables.ods]
2016-11-06 Finalized pin map, moved main FW folder but leaving the original pre-UART prompt addition
    [RegisterMap.ods]
2016-11-06 Getting very close to release, tests looking good but failsafe isn't quite there
    [RegisterMap.ods, TP1.ods, TP2.ods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]
2016-11-07 Everything is broken
    [RegisterMap.ods]
2016-11-10 Exported PDF datasheet
    [RegisterMap.ods]
2016-11-18 Squashed 'Libraries/Arduino/' content from commit a6f2818
    git-subtree-dir: Libraries/Arduino
    git-subtree-split: a6f281868b108a5d845209acaeb743df012d8111
2017-05-04 Added enable pin at U2.5, readable by status_1 at 0x77, bit 2
2017-06-21 Created FW version 07 which is compatible with the moto_bit and the serial controlled motor driver. FW ID can be read at address 0x00 and the enable pin state at 0x77, bit 2
2017-06-22 bug fix on release
    [slaveEnumeration.c]
2017-06-22 Updated documentation and config header for moto:bit application. Bit position of 0x77 for reading enable state moved from b2 to b4
    [RegisterMap.ods, Serial Controlled Motor Driver.sch]

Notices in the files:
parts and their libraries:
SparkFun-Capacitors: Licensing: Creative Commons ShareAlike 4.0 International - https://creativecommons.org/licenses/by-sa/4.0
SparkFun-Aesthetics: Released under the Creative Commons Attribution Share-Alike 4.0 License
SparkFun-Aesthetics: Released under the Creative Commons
